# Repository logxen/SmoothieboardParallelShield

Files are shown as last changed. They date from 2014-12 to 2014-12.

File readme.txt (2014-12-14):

Smoothieboard Parallel Shield

Licensed under the CERN Open Hardware License version 1.2

This pcb makes connecting a Parallel CNC Machine and the common Reprap Discount GLCD Screen to a Smoothieboard very easy. It has an optional footprint for a 5V regulator to make sure the screen gets enough power. Information on how to configure Smoothieware for use with a display panel can be found here: http://smoothieware.org/panel

Bill of Materials:

1x DB25 R/A PTH connector (such as TE Connectivity 1734350-1)
3x TXS0108E level shifter ic (or 3x 0R 0603 8 resistor networks)
2x SK310A (or similar) SMA schottky diodes to protect voltage inputs from reverse flow
8x 0.1uF 0603 capacitors
1x R78E5.0-0.5 switching voltage regulator
2x 2x5 0.1" shrouded male header
1x 1x3 0.1" male breakaway header
1x 0.1" jumper
2x 2x3 0.1" female header
2x 1x3 0.1" female header
6x 1x4 0.1" female header
1x 1x5 0.1" female header
1x 1x6 0.1" stacking female header (or just a 1x3 female header)

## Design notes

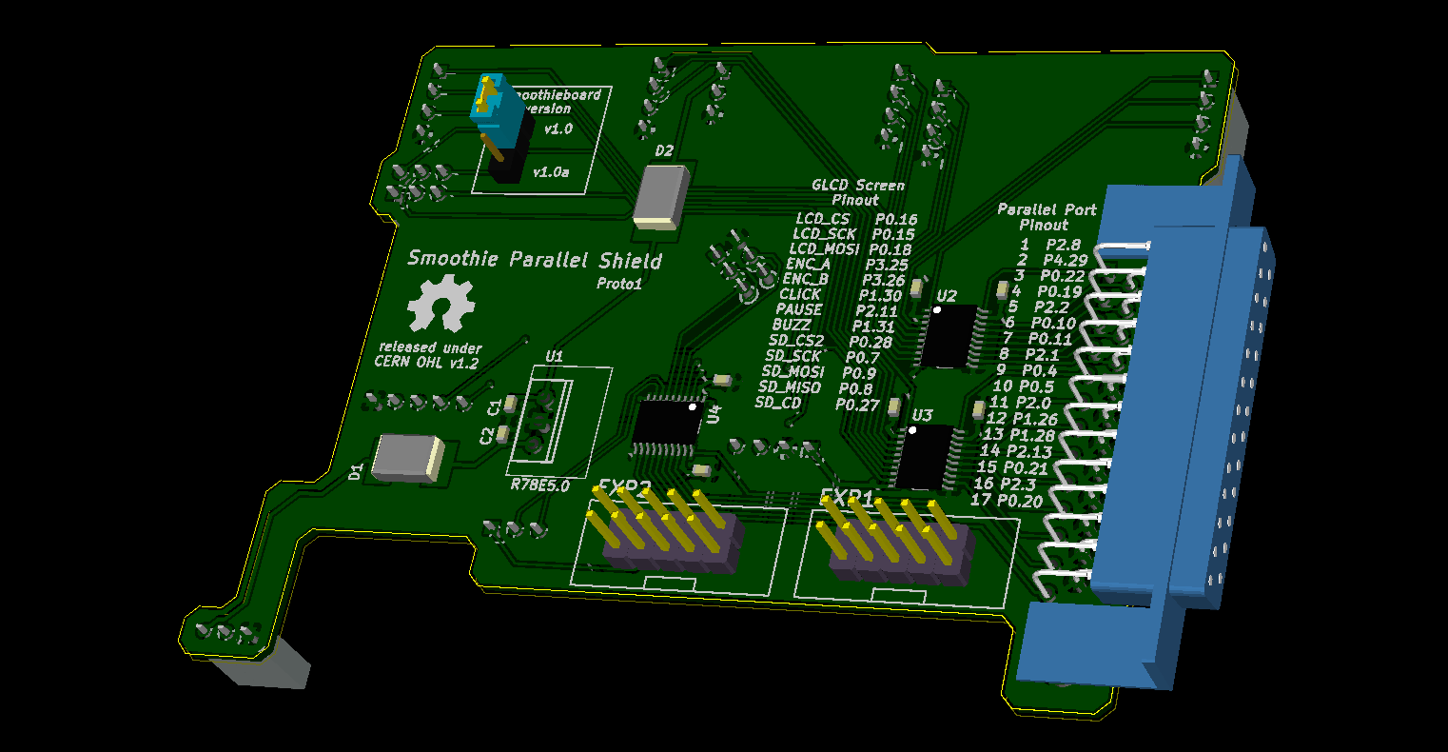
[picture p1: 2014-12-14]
SmoothieParallelShield-Proto1.png

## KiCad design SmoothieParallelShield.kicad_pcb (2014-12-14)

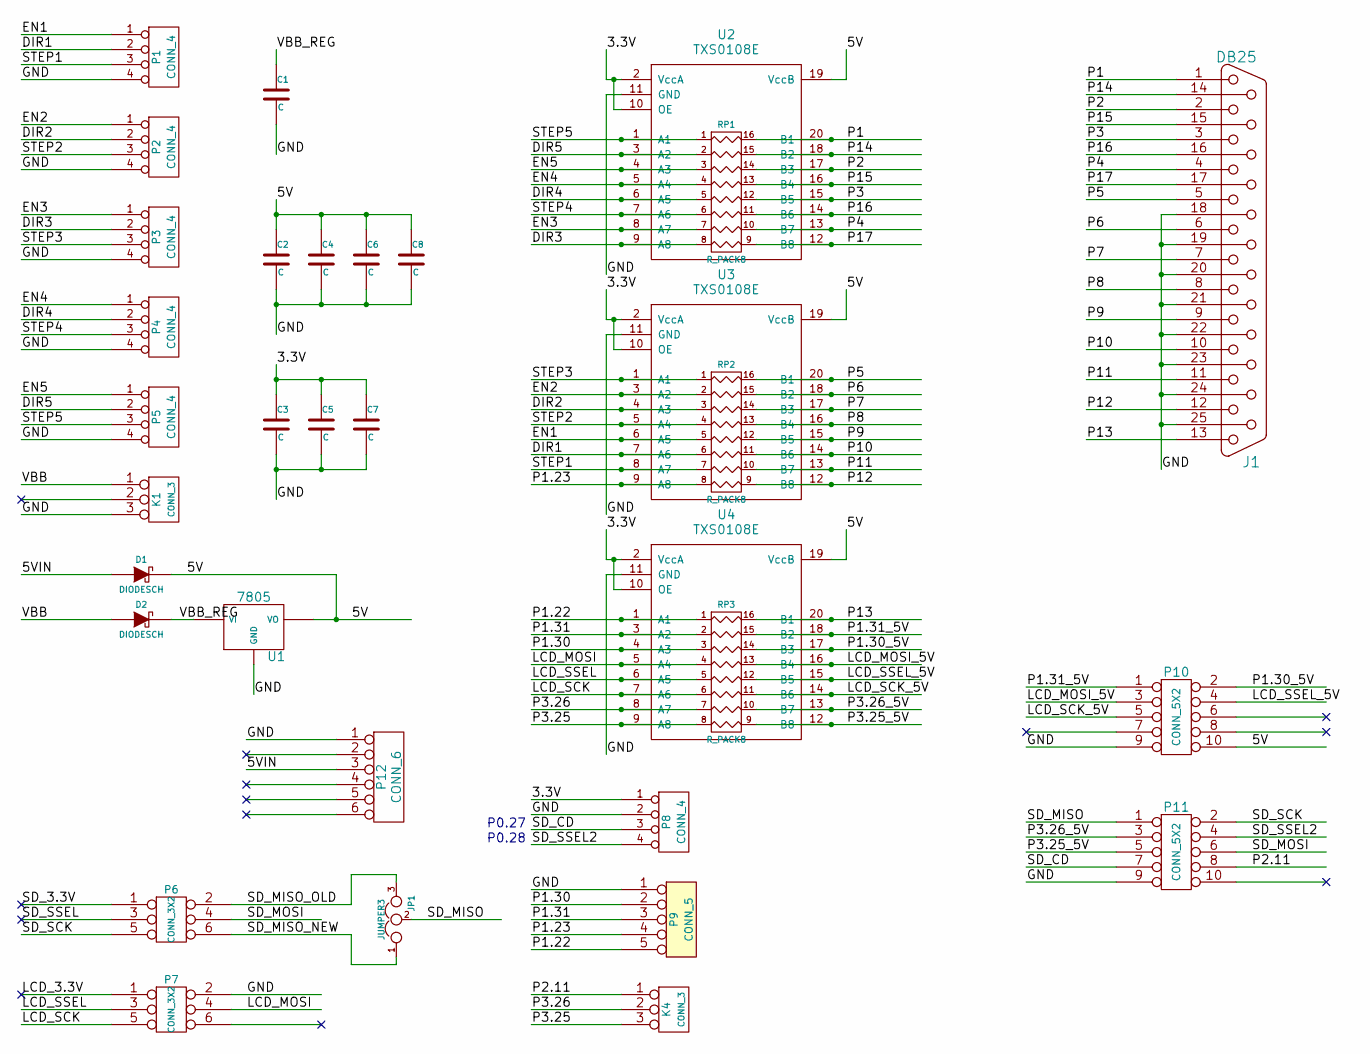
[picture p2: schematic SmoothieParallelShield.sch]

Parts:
C1, C2, C3, C4, C5, C6, C7, C8: C
D1, D2: DIODESCH
J1: DB25
JP1: JUMPER3
K1, K4: CONN_3
P1, P2, P3, P4, P5, P8: CONN_4
P6, P7: CONN_3X2
P9: CONN_5
P10, P11: CONN_5X2
P12: CONN_6
RP1, RP2, RP3: R_PACK8
U1: 7805
U2, U3, U4: TXS0108E

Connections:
/3.3V: C3.1, C5.1, C7.1, P8.1, U2.2 (VccA), U2.10 (OE), U3.2 (VccA), U3.10 (OE), U4.2 (VccA), U4.10 (OE)
/5V: C2.1, C4.1, C6.1, C8.1, D1.2 (K), P10.10, U1.VO, U2.19 (VccB), U3.19 (VccB), U4.19 (VccB)
/5VIN: D1.1 (A), P12.3
/DIR1: P1.2, RP2.6, U3.7 (A6)
/DIR2: P2.2, RP2.3, U3.4 (A3)
/DIR3: P3.2, RP1.8, U2.9 (A8)
/DIR4: P4.2, RP1.5, U2.6 (A5)
/DIR5: P5.2, RP1.2, U2.3 (A2)
/EN1: P1.1, RP2.5, U3.6 (A5)
/EN2: P2.1, RP2.2, U3.3 (A2)
/EN3: P3.1, RP1.7, U2.8 (A7)
/EN4: P4.1, RP1.4, U2.5 (A4)
/EN5: P5.1, RP1.3, U2.4 (A3)
/GND: C1.2, C2.2, C3.2, C4.2, C5.2, C6.2, C7.2, C8.2, J1.18, J1.19, J1.20, J1.21, J1.22, J1.23, J1.24, J1.25, K1.3, P1.4, P2.4, P3.4, P4.4, P5.4, P7.2, P8.2, P9.1, P10.9, P11.9, P12.1, U1.GND, U2.11 (GND), U3.11 (GND), U4.11 (GND)
/LCD_MOSI: P7.4, RP3.4, U4.5 (A4)
/LCD_MOSI_5V: P10.3, RP3.13 (R4), U4.16 (B4)
/LCD_SCK: P7.5, RP3.6, U4.7 (A6)
/LCD_SCK_5V: P10.5, RP3.11 (R6), U4.14 (B6)
/LCD_SSEL: P7.3, RP3.5, U4.6 (A5)
/LCD_SSEL_5V: P10.4, RP3.12 (R5), U4.15 (B5)
/P1: J1.1, RP1.16 (R1), U2.20 (B1)
/P1.22: P9.5, RP3.1, U4.1 (A1)
/P1.23: P9.4, RP2.8, U3.9 (A8)
/P1.30: P9.2, RP3.3, U4.4 (A3)
/P1.30_5V: P10.2, RP3.14 (R3), U4.17 (B3)
/P1.31: P9.3, RP3.2, U4.3 (A2)
/P1.31_5V: P10.1, RP3.15 (R2), U4.18 (B2)
/P2: J1.2, RP1.14 (R3), U2.17 (B3)
/P2.11: K4.1, P11.8
/P3: J1.3, RP1.12 (R5), U2.15 (B5)
/P3.25: K4.3, RP3.8, U4.9 (A8)
/P3.25_5V: P11.5, RP3.9 (R8), U4.12 (B8)
/P3.26: K4.2 (PM), RP3.7, U4.8 (A7)
/P3.26_5V: P11.3, RP3.10 (R7), U4.13 (B7)
/P4: J1.4, RP1.10 (R7), U2.13 (B7)
/P5: J1.5, RP2.16 (R1), U3.20 (B1)
/P6: J1.6, RP2.15 (R2), U3.18 (B2)
/P7: J1.7, RP2.14 (R3), U3.17 (B3)
/P8: J1.8, RP2.13 (R4), U3.16 (B4)
/P9: J1.9, RP2.12 (R5), U3.15 (B5)
/P10: J1.10, RP2.11 (R6), U3.14 (B6)
/P11: J1.11, RP2.10 (R7), U3.13 (B7)
/P12: J1.12, RP2.9 (R8), U3.12 (B8)
/P13: J1.13, RP3.16 (R1), U4.20 (B1)
/P14: J1.14, RP1.15 (R2), U2.18 (B2)
/P15: J1.15, RP1.13 (R4), U2.16 (B4)
/P16: J1.16, RP1.11 (R6), U2.14 (B6)
/P17: J1.17, RP1.9 (R8), U2.12 (B8)
/SD_CD: P8.3, P11.7
/SD_MISO: JP1.2, P11.1
/SD_MISO_NEW: JP1.1, P6.6
/SD_MISO_OLD: JP1.3, P6.2
/SD_MOSI: P6.4, P11.6
/SD_SCK: P6.5, P11.2
/SD_SSEL2: P8.4, P11.4
/STEP1: P1.3, RP2.7, U3.8 (A7)
/STEP2: P2.3, RP2.4, U3.5 (A4)
/STEP3: P3.3, RP2.1, U3.1 (A1)
/STEP4: P4.3, RP1.6, U2.7 (A6)
/STEP5: P5.3, RP1.1, U2.1 (A1)
/VBB: D2.1 (A), K1.1
/VBB_REG: C1.1, D2.2 (K), U1.VI

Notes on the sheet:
P0.27
P0.28

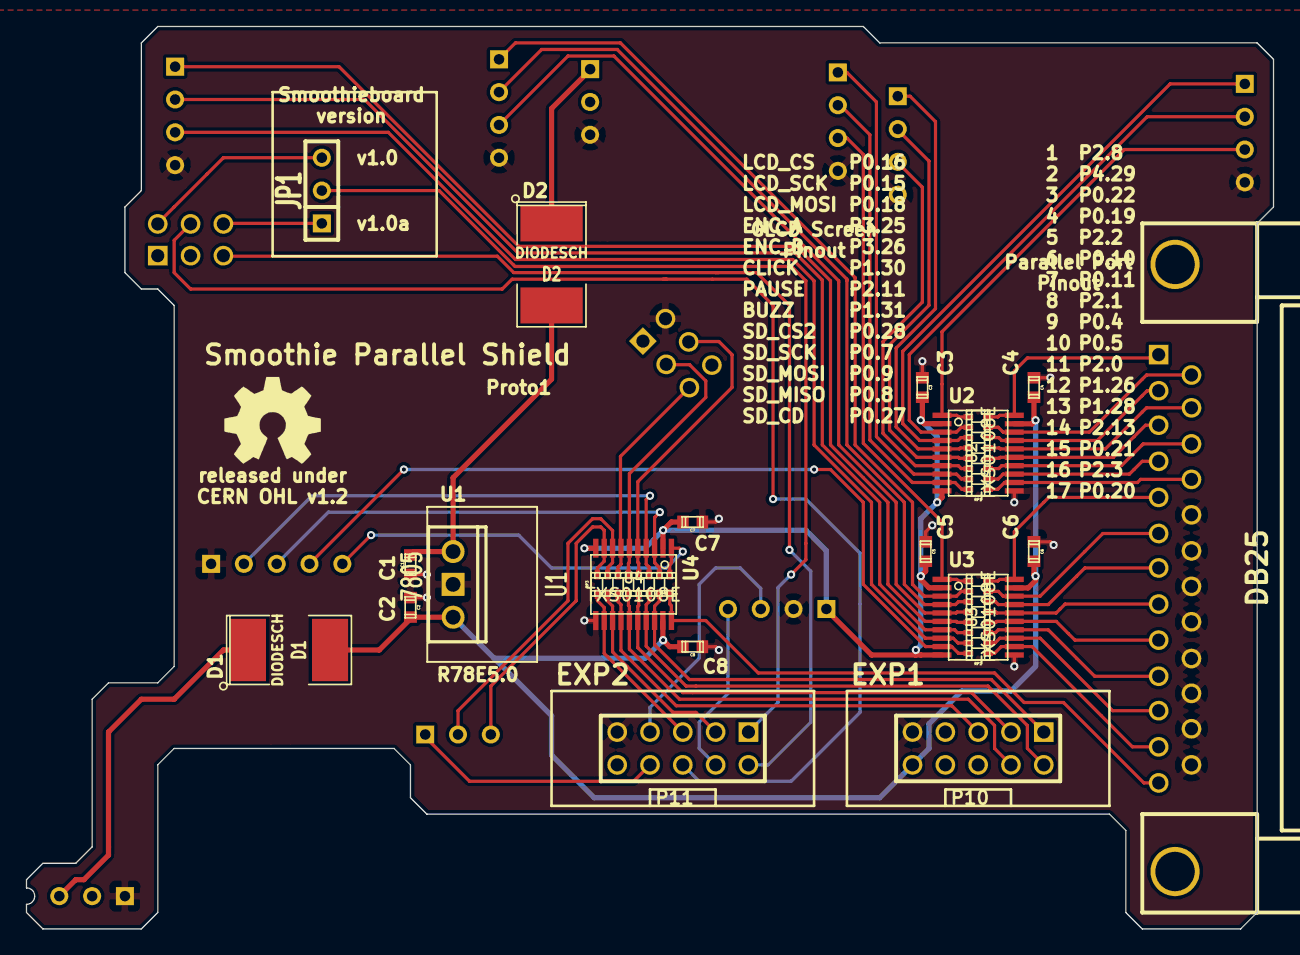
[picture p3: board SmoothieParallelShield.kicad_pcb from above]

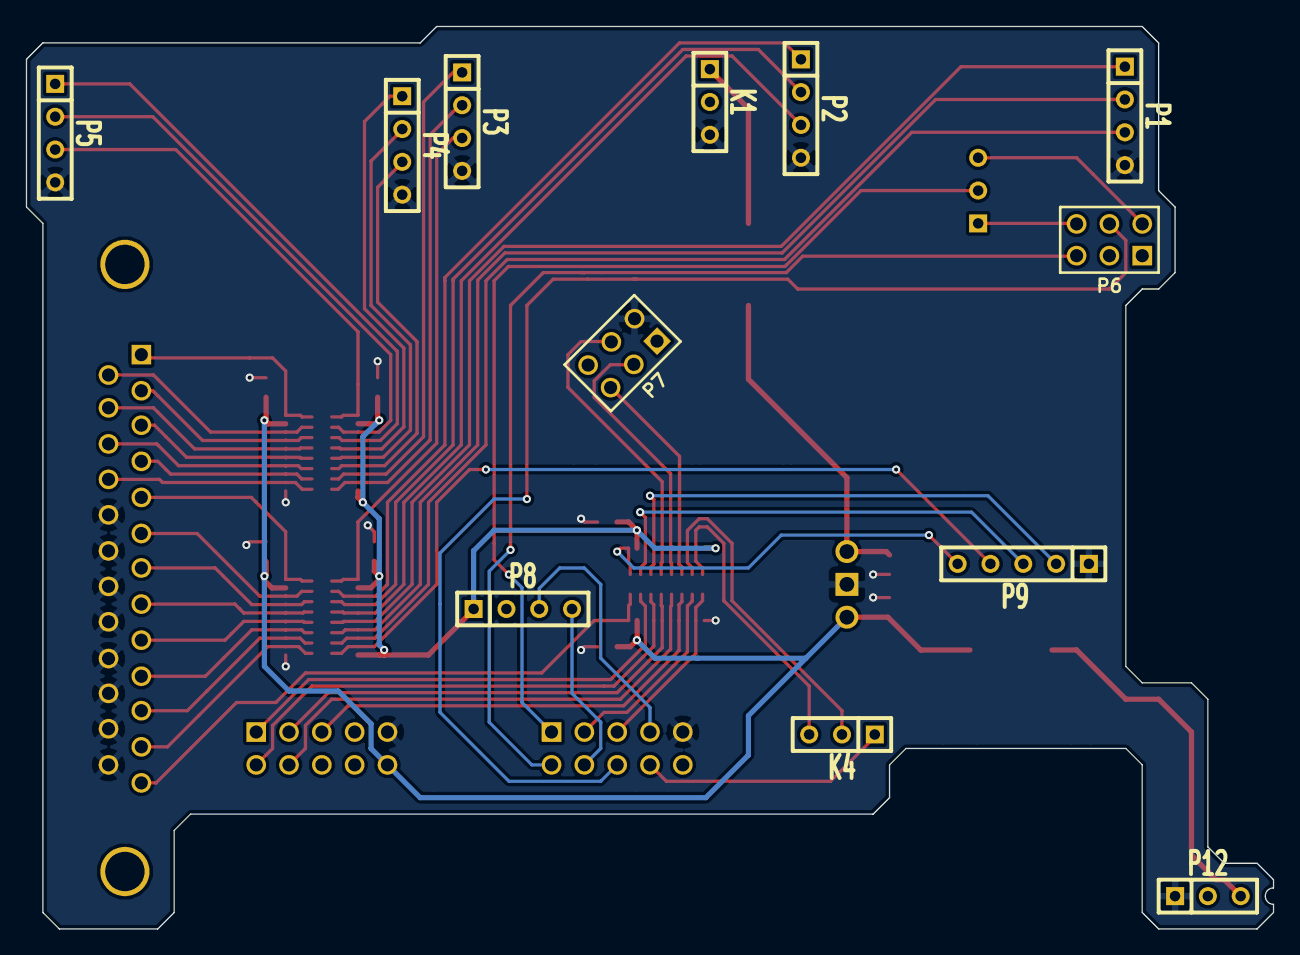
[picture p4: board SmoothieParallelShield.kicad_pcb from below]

Board: 2 copper layers, 96.5 x 69.9 mm, 34 parts (12 on the bottom side), 62 nets.

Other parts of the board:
VAL: REF; OSHW-LOGO_SMALL

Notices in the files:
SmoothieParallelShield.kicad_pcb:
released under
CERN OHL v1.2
